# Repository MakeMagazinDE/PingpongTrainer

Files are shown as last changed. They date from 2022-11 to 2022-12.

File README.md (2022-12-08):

GitHub Logo

Maker Media GmbH

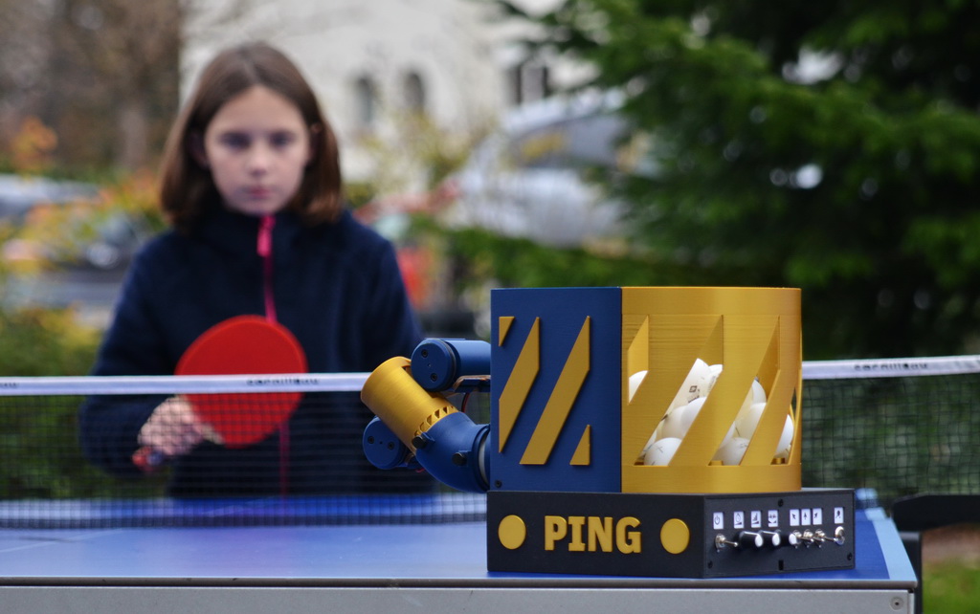
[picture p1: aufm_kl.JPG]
Aufmacher


# Pingpong-Trainingroboter

Tischtennis beinhaltet alles, was ein gutes Freizeitspiel ausmacht: Geschick und Bewegung, Wettbewerb und Spaß, Action und Geselligkeit. Wenn letztere einmal ausfällt, hilft unser Pingpong-Trainingsroboter, der automatisch Bälle in wechselnde Richtungen verschießt.

**Bitte beachten Sie:** Unter **Material** steht im Artikel *Arduino Uno*. Benutzt wird aber ein **Arduino Nano**!

Eine Schritt-für-Schritt-Bauanleitung steht als PDF zu Verfügung, da der Artikel aus Platzgründen nicht alle Aspekte des Aufbaus behandeln konnte.

Stückliste und Verdrahtung siehe Excel-Sheet **Bauteile_und_Verbindungen.xlsx** (Datei mit als "View Raw" oder "Download" herunterladen). Die Excel-Arbeitsmappe wurde auch als PDF konvertiert, ist hier aber unter Umständen nicht mehr gut lesbar.

Ein Video vom Pingpong-Trainingsroboter ist inzwischen hier auf Youtube zu finden: https://youtu.be/tKqPbJfTlDg

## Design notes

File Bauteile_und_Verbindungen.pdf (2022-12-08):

Einkaufsliste

Material | Anzahl | Einzelpreis | Total | Lieferant | Link | Hinweis
Servo MG90s, 180° (digital) | 1 € | 1.99 € | 1.99 AliExpress | https://de.aliexpress.co (https://de.aliexpress.com/item/1005003620828597.html?curPageLogUid=8dz3BZQSF9wu) Bestelldetails siehe Bild.
DC Motor 380, 12V/8'000 RPM, 24V/16'000 RMP | | 2 € | 0.61 € | 1.22 AliExpress | https://de.aliexpress.co (https://de.aliexpress.com/item/32664338955.html)
DC Motor S30K, 12V/14 RPM | 1 € | 1.34 € | 1.34 AliExpress | https://de.aliexpress.co (https://de.aliexpress.com/item/32819069437.html) Bestelldetails siehe Bild
Potentiometer WH148, 10kOhm | 3 | € | 1.14 AliExpress | https://de.aliexpress.co (https://de.aliexpress.com/item/4000971762879.html) 5 Stück pro Los -> 1 bestellen
Mini Kippschalter, MTS-102 SPDT | 4 | € | 0.96 AliExpress | https://de.aliexpress.co (https://de.aliexpress.com/item/32424649963.html) 5 Stück pro Los -> 1 bestellen
Taster mit LED, grün, ohne Symbol, 12mm, Momentary self-reset, 5V | 1 € | 0.75 € | 0.75 AliExpress | https://de.aliexpress.co (https://de.aliexpress.com/item/4001291695467.html) Bestelldetails siehe Bild
NANO Expansion Prototyp Schild I/O R3 | 1 € | 1.06 € | 1.06 AliExpress | https://de.aliexpress.co (https://de.aliexpress.com/item/32836369656.html) Farbe egal. Die rote Version finde ich etwas übersichtlicher, da die Pins
| | | | | | farbcodiert sind.
Terminal Block KF128-2.54, 4 Pins | 1 € | 1.47 € | 1.47 AliExpress | https://de.aliexpress.co Es kann auch ein 6 Pin Terminal bestellt werden, um gleich die ganze Reihe
| | | | | | der Steckplätze zu bestücken. 5 Stücke pro Los -> 1 bestellen
Arduino Nano 328p mit angelöteten Pins | 1 € | 4.42 € | 4.42 AliExpress | https://de.aliexpress.co (https://de.aliexpress.com/item/1005003041312268.html?ad_pvid=202207231457511969517035539440007786855_3&s=p) Empfohlen: Version 328p mit USB-C und bereits angelöteten Pins.
| | | | | | Bestelldetails siehe Bild.
Motortreiber L298N, rot | 2 € | 0.89 € | 1.78 AliExpress | https://de.aliexpress.co (https://de.aliexpress.com/item/32969673726.html) Die Schublade hat nur Bohrlöcher passend für die rote Version!
Micro Limit Switch, ZW12-B | 1 € | 0.76 € | 0.76 AliExpress | https://de.aliexpress.co (https://de.aliexpress.com/item/10000284039075.html) 5 Stücke pro Los -> 1 bestellen
Step Up Converter MT3608 | 1 € | 1.94 € | 1.94 AliExpress | https://de.aliexpress.co (https://de.aliexpress.com/item/4001066566291.html) USB nicht notwendig.
Batteriehalter, 6xAA | | 1 € | 0.22 € | 0.22 AliExpress | https://de.aliexpress.co (https://de.aliexpress.com/item/1005002013461693.html)
Dichtungsring (NBR O-Ring) OD 40mm, ID 28mm, 6mm, black | 2 | € | 1.89 AliExpress | https://de.aliexpress.co 5 Stücke pro Los -> 1 bestellen
Kabel DuPont, beidseitig female/Buchsen, 30cm | | | € | 1.44 AliExpress | https://de.aliexpress.co (https://de.aliexpress.com/item/32639799546.html)
Kabel DuPont, beidseitig female/Buchsen, 10cm | € | 0.93 AliExpress | https://de.aliexpress.co (https://de.aliexpress.com/item/32422441283.html) Im Verbindungsplan stehen die Kabellängen. Da einige Kabel einseitig verlötet
| | | | | | werden, muss bei einigen Verbindungen das andere Steckerende abgetrennt werden. Die Potentiometer könnten statt mit einem einadrigen auch mit einem dreiadrigen DuPont-Kabel verbunden werden.
Rändelschraube M3x8 | 2 | € | 2.14 AliExpress | https://de.aliexpress.co (https://de.aliexpress.com/item/1005001434315050.html?curPageLogUid=SsNZ1RpAGzNE) 5 Stück pro Los -> 1 bestellen. Notfalls ginge es auch mit 2 "normalen"
| | | | | | Zylinderkopfschrauben.
Schraube M3x8, Senkkopf | 15 | € | - | https://de.aliexpress.co (https://de.aliexpress.com/item/32934186482.html)
Schraube M3x8, Zylinderkopf | 25 | € | - | https://de.aliexpress.co (https://de.aliexpress.com/item/32810872544.html)
Schraube M2 | 2 | € | - | Schraubenlänge ca. 6 mm, oftmals werden die Schrauben mit dem Servo
| | | | | | mitgeliefert.
Schraube M2.5 | 3 | € | - | Schraubenlängen:
| | | | | | 1x ca. 6 mm (oftmals wird die Schrauben mit dem Servo mitgeliefert) 2x ca. 12mm (kürzer geht auch)
Mutter M3, vierkant | 30 | € | - | https://de.aliexpress.co (https://de.aliexpress.com/item/1005001612157787.html)
Gummibänder | 4 | € | -
Litzen (rot, schwarz) | € | -
Ping Pong Bälle | € | -
Stück eines alten Fahrradschlauchs | € | -
€ | 25.45 | 22

Viele der M3 Schrauben passen auch, wenn diese länger oder kürzer sind. Damit eine allfällige Schraubenbestellung aber einfacher geht, können alle M3 Schrauben in 8mm Länge bestellt werden. Die passen immer!

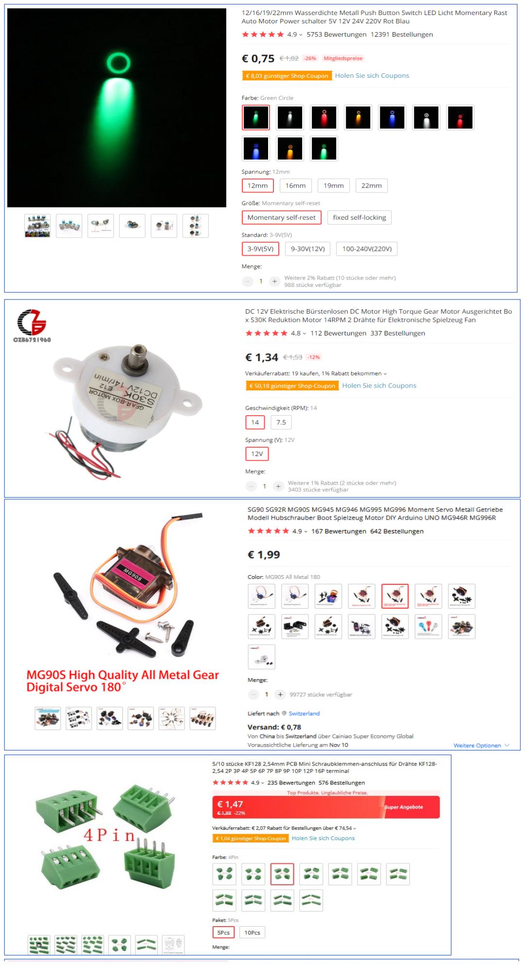
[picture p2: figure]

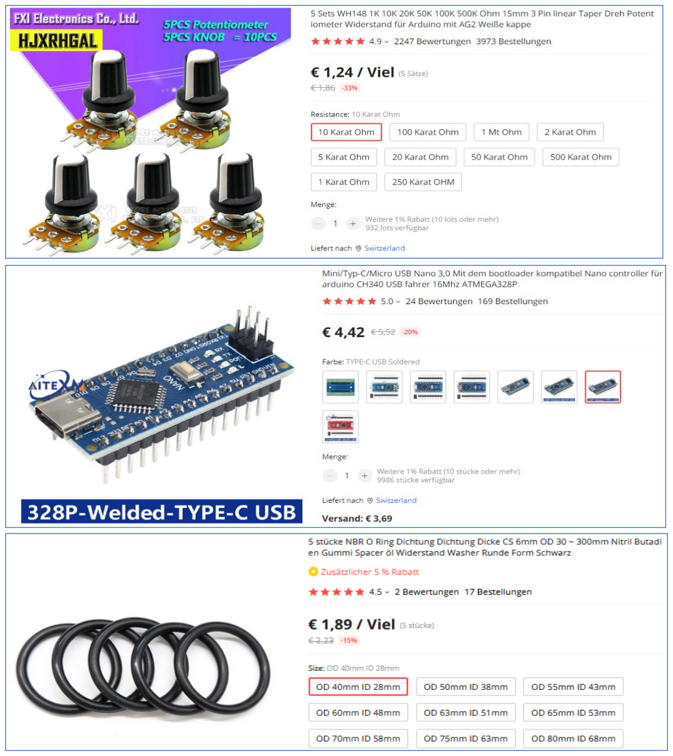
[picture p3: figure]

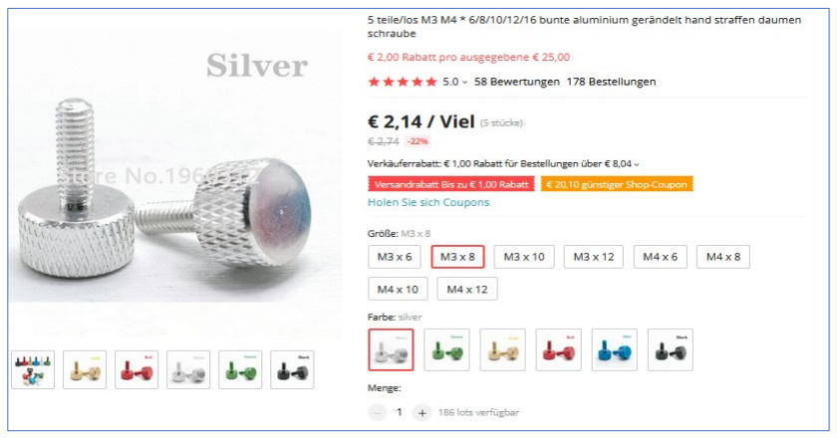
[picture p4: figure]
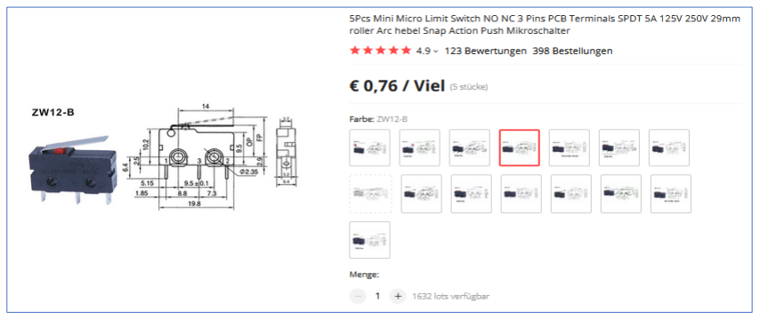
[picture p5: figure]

## Druckbare Bauteile

STL-Datei | 3MF-Datei | Farbvorschlag | Hinweis | Gewicht (g)
AdapterMicroswitch.stl | AdapterMicroswitch.3mf | Schwarz | | 4
AdapterScheibe.stl | AdapterScheibe.3mf | Gelb | | 4
Basis.stl | Basis.3mf | Schwarz | | 308
Biegung 25 Grad.stl | Biegung.3mf | Blau | Optionales Bauteil für flache Bälle. | 20
Biegung 40 Grad.stl | Biegung.3mf | Blau | | 23
Biegung 55 Grad.stl | Biegung.3mf | Blau | Optionales Bauteil für hohe Bälle. | 26
Deko[X].stl | Deko.3mf | Gelb | | 13
Ecke.stl | Ecke.3mf | Blau | | 95
Korb.stl | Korb.3mf | Gelb | Mit Rand drucken für bessere Haftung. | 150
Lauf.stl | Lauf.3mf | Gelb | | 48
Motorschalen[XX].stl, Motoreinsatz.stl | Motorbefestigung.3mf | Blau | Ausrichtung: Runde Öffnung der
| | | Motorbefestigung auf Druckbett liegend.
| | | Motoreinsatz 2x drucken. | 54
Rad[X].stl | Rad.3mf | Blau | Stützen unter den Bohrlöchern bei den
| | | Schraubköpfen von Rad1.stl empfohlen.
| | | Layerhöhe 0.15mm empfohlen. Oberfläche
| | | bügeln empfohlen. Alles zweimal drucken! | 9
Scheibe.stl | Scheibe.3mf | Gelb | | 33
SchriftzugSeite.stl | Schriftzug.3mf | Gelb | Zweimal ausdrucken! | 9
SchriftzugVorne.stl | Schriftzug.3mf | Gelb | | 4
SchubladeBlende.stl | SchubladeBlende.3mf | Schwarz | Ausrichtung: Unbedingt stehend drucken!
| | | Die Blende hat einen kaum sichtbaren
| | | Papiereinschub. Bei falscher
| | | Druckausrichtung lässt sich das Papier für die
| | | Labels später nicht dazwischenschieben.
| | | Drucken eines Randes (Brim) für bessere
| | | Haftung empfohlen. | 33
SchubladeBoden.stl | SchubladeBoden.3mf | Schwarz | | 85
Schwenkarm.stl | Schwenkarm.3mf | Blau | | 10
Servoarm.stl | Servoarm.3mf | Schwarz | Stützen unter dem Bohrloch empfohlen. | 1
Zufuehrung.stl | Zufuehrung.3mf | Blau | | 54
Ergebnis | | | | 983

Generelle Druckanweisungen, anwendbar sofern nicht anders ausgewiesen:
- PLA Filament verwenden
- Layerhöhe 0.3mm / Düsendurchmesser 0.4mm (Standard-Düse)
- Ausrichtung der Bauteile: Siehe Screenshots in der Bauanleitung (Anhang 1)
- Keine Stützen notwendig
- Standardeinstellungen des Slicers führen in der Regel zu einem guten Ergebnis

Für alle Bauteile stehen die 3MF-Dateien zur Verfügung. Wenn du diese Dateien im PrusaSlicer öffnest, ist alles bereits für dich eingestellt. Du brauchst nur noch zu slicen und zu drucken.

Tipps:
- Je nach Filament treten die Drucknähte störend in Erscheinung. Ein schöneres Ergebnis kann immer erzielt werden, wenn die Drucknähte auf eine Kante ausgerichtet sind.
- Innenliegende, kaum sichtbare Bauteile (z.B. AdapterMicroswitch, AdapterScheibe, Servoarm, Schubladenboden) können auch mit Filamentresten beliebiger Farbe gedruckt werden, ohne das Design zu beinträchtigen.
- Basis.stl: Der Druck dieses Bauteils ist etwas anfällig für Warping. Sollten sich die Ecken am Druckboden unschön wölben, sollten entsprechende Massnahmen gegen Verzug angewandt werden. (Onkel Google hilft weiter: Stichwort "3D Druck Warping")
- Stützen unter Bohrlöchern (Servoarm.stl, Rad1.stl) können in der Regel ganz einfach entfernt werden, indem man diese von der anderen Seite durch das Bohrloch herausdrückt.
- Bauteile "Biegung xx Grad.stl": Die angegebene Anzahl Schrauben und Muttern basiert auf der Verwendung von nur einer dieser Bauteilvarianten. Ich empfehle, vorerst nur die Variante mit dem 40 Grad-Winkel zu drucken und zu nutzen. Wer die beiden anderen Winkel für die Schussabgabe später auch verwenden möchte, sollte bei der Materialbestellung zusätzliche Schrauben, Muttern und Rändelschrauben miteinrechnen.
- Beim Druck von Dekoelementen und Schriftzügen drucke ich vielfach nur eine (1) vertikale Konturhülle und lege die Objekte mit der später sichtbaren Aussenseite auf das glatte Druckbett.
- "Elefantenfüsse" können die Passgenauigkeit der Bauteile erschweren. Deshalb sollte eine entsprechende Elefantenfuss-Kompensation beim Druck angewendet werden. (Bei PLA genügt meistens 0.1mm.)
- Wer Filament sparen möchte, kann insbesondere bei den horizontalen, massiven, grossflächigen Schichten einsparen (z.B. bei der Scheibe oder beim Schubladenboden nur zwei massive Bodenschichten drucken.)

## Verbindungsplan

Nr. | Bauteil A | Anschluss Bauteil A | Lötv. A | Verbindung | Lötv. B | Anschluss Bauteil B | Bauteil B | Hinweis
0 Terminal Block KF128 | | Alle Pins | x | Terminal Block auf das Expansion Board stecken und Pins anlöten. | x | VCC, G, G, VIN | NANO I/O Expansion Board | Ist das Terminal angelötet, dann sind die Labels der Anschlüsse auf dem Board nicht mehr sichtbar. Deshalb wird empfohlen, die Anschlüsse am Terminal mit einem Stift anzuschreiben.
1 Batteriefach 6AA | | rote Ader (+) | x | Ader des Batteriefachs direkt an Schalter anlöten. | x | Mittlerer Kontakt | Mini Kippschalter MTS-102 SPDT (Einschalter)
2 Batteriefach 6AA | | schwarze Ader (-) | x | Ader des Batteriefachs direkt an Converter anlöten. | x | VIN- | StepUp Converter MT3608
3 Mini Kippschalter MTS-102 SPDT | (Einschalter) | NO | x | 12cm Kabel (rot) beidseitig anlöten. An diesem Anschluss des Kippschalters werden zwei Verbindungen angebracht: Nr. 3 und 4. --> Am besten gleichzeitig anlöten! | x | VIN+ | StepUp Converter MT3608
4 Mini Kippschalter MTS-102 SPDT | (Einschalter) | NO | x | 20cm Kabel (rot) an Schalter anlöten und am Schraubterminal einschrauben. An diesem Anschluss des Kippschalters werden zwei Verbindungen angebracht: Nr. 3 und 4. --> Am besten gleichzeitig anlöten! | | VIN (Schraubterminal) | NANO I/O Expansion Board
5 Mini Kippschalter MTS-102 SPDT | (Schussrichtung links) | NO | x | 10cm Kabel, DuPont-Buchse einseitig: An Schalter anlöten und am Pin des Boards einstecken. | | A2 (D16) | NANO I/O Expansion Board
6 Mini Kippschalter MTS-102 SPDT | (Schussrichtung links) | Mittlerer Kontakt | x | 10cm Kabel (schwarz), DuPont-Buchse einseitig: An Schalter anlöten und am Pin des Boards einstecken. | | GND | NANO I/O Expansion Board
7 Mini Kippschalter MTS-102 SPDT | (Schussrichtung mitte) | NO | x | 10cm Kabel, DuPont-Buchse einseitig: An Schalter anlöten und am Pin des Boards einstecken. | | A3 (D17) | NANO I/O Expansion Board
8 Mini Kippschalter MTS-102 SPDT | (Schussrichtung mitte) | Mittlerer Kontakt | x | 10cm Kabel (schwarz), DuPont-Buchse einseitig: An Schalter anlöten und am Pin des Boards einstecken. | | GND | NANO I/O Expansion Board
9 Mini Kippschalter MTS-102 SPDT | (Schussrichtung rechts) | NO | x | 10cm Kabel, DuPont-Buchse einseitig: An Schalter anlöten und am Pin des Boards einstecken. | | A4 (D18) | NANO I/O Expansion Board
10 Mini Kippschalter MTS-102 SPDT | (Schussrichtung rechts) | Mittlerer Kontakt | x | 10cm Kabel (schwarz), DuPont-Buchse einseitig: An Schalter anlöten und am Pin des Boards einstecken. | | GND | NANO I/O Expansion Board
11 Micro Limit Switch ZW12-B (Sensor für | Ballvorschub) | NO | x | 40cm Kabel, DuPont-Buchse einseitig: An Schalter anlöten und am Pin des Boards einstecken. Kabel am Micro Limit Switch unbedingt so anlöten, dass diese direkt nach hinten geführt werden können! (Siehe Abbildung im Anhang 2 der Bauanleitung.) | | A0 | NANO I/O Expansion Board | 30cm Kabel wäre auch knapp ausreichend. Die Schublade lässt sich dann aber nicht mehr vollständig ausziehen.
12 Micro Limit Switch ZW12-B (Sensor für | Ballvorschub) | C | x | 40cm Kabel (schwarz), DuPont-Buchse einseitig: An Schalter anlöten und am Pin des Boards einstecken. Kabel am Micro Limit Switch unbedingt so anlöten, dass diese direkt nach hinten geführt werden können! Der Platz im Bauteil AdapterMicroswitch ist knapp! (Siehe Abbildung im Anhang 2 der Bauanleitung.) | | GND | NANO I/O Expansion Board | 30cm Kabel wäre auch knapp ausreichend. Die Schublade lässt sich dann aber nicht mehr vollständig ausziehen.
13 Momentary Switch mit LED (LED) | | Plus (+) | x | 10cm Kabel (rot), DuPont-Buchse einseitig: An Schalter anlöten und am Pin des Boards einstecken. | | D12 | NANO I/O Expansion Board
14 Momentary Switch mit LED (LED) | | Minus (-) | x | 10cm Kabel (schwarz), DuPont-Buchse einseitig: An Schalter anlöten und am Pin des Boards einstecken. | | GND | NANO I/O Expansion Board
15 Momentary Switch mit LED (Startknopf) | | (ohne Beschriftung) | x | 10cm Kabel, DuPont-Buchse einseitig: An Schalter anlöten und am Pin des Boards einstecken. | | A1 | NANO I/O Expansion Board
16 Momentary Switch mit LED (Startknopf) | | (ohne Beschriftung) | x | 10cm Kabel (schwarz), DuPont-Buchse einseitig: An Schalter anlöten und am Pin des Boards einstecken. | | GND | NANO I/O Expansion Board
17 Servo MG90s | GND (braune Ader) | Stecker des Servos direkt mit den Pins des Boards verbinden. | GND | NANO I/O Expansion Board

18 Servo MG90s | V (rote Ader) | | Stecker des Servos direkt mit den Pins des Boards verbinden. | | V | NANO I/O Expansion Board
19 Servo MG90s | Signal (gelbe Ader) | | Stecker des Servos direkt mit den Pins des Boards verbinden. | | D5 | NANO I/O Expansion Board
20 Motortreiber L298N - A | VCC (Schraubterminal) | | 15cm Kabel (rot): Am Terminal des Motortreibers einschrauben und am Converter anlöten. | x | VOUT+ | StepUp Converter MT3608 | Am Anschluss des Motortreibers werden zwei Kabel angebracht -> Nr. 43
21 NANO I/O Expansion Board | GND (Schraubterminal) | | 15cm Kabel (schwarz): Am Terminal des Boards einschrauben und am Converter anlöten. | x | VOUT- | StepUp Converter MT3608 | Das Schraubterminal des Microcontrollers hat zwei GND Anschlüsse. Nimm einfach einen freien Platz.
22 Motortreiber L298N - A | GND (Schraubterminal) | | 5cm Kabel (schwarz): Beidseitig an den Terminals einschrauben. | | GND (Schraubterminal) | NANO I/O Expansion Board | Das Schraubterminal des Microcontrollers hat zwei GND Anschlüsse. Nimm einfach einen freien Platz. Am Anschluss des Motortreibers werden zwei Kabel angebracht -> Nr. 44
23 Motortreiber L298N - A | 5V (Schraubterminal) | | 5cm Kabel (rot): Beidseitig an den Terminals einschrauben. | | 5V (Schraubterminal) | NANO I/O Expansion Board | Am Anschluss des Motortreibers werden zwei Kabel angebracht -> Nr. 45
24 Motortreiber L298N - A | OUT1 (Schraubterminal) | | 60cm Kabel (rot): Am Terminal des Motortreibers einschrauben und am Motor anlöten. | x | Plus | DC Motor 380 (oben)
25 Motortreiber L298N - A | OUT2 (Schraubterminal) | | 60cm Kabel (schwarz): Am Terminal des Motortreibers einschrauben und am Motor anlöten. | x | Minus | DC Motor 380 (oben)
26 Motortreiber L298N - A | OUT4 (Schraubterminal) | | Rote Ader des Motors verlängern auf 30 cm. Verbindungsstelle mit Schrumpfschlauch isolieren. Am Terminal des Motortreibers einschrauben. | x | rote Ader | DC Motor S30K (Vorschub)
27 Motortreiber L298N - A | OUT3 (Schraubterminal) | | Schwarze Ader des Motors verlängern auf 30 cm. Verbindungsstelle mit Schrumpfschlauch isolieren. Am Terminal des Motortreibers einschrauben. | x | schwarze Ader | DC Motor S30K (Vorschub)
28 Motortreiber L298N - A | ENA | | 10cm Kabel beidseitig mit DuPont-Buchse: Pins beidseitig verbinden. | | D11 | NANO I/O Expansion Board
29 Motortreiber L298N - A | IN1 | | 10cm Kabel beidseitig mit DuPont-Buchse: Pins beidseitig verbinden. | | D9 | NANO I/O Expansion Board
30 Motortreiber L298N - A | IN2 | | 10cm Kabel beidseitig mit DuPont-Buchse: Pins beidseitig verbinden. | | D10 | NANO I/O Expansion Board
31 Motortreiber L298N - A | IN3 | | 10cm Kabel beidseitig mit DuPont-Buchse: Pins beidseitig verbinden. | | D7 | NANO I/O Expansion Board
32 Motortreiber L298N - A | IN4 | | 10cm Kabel beidseitig mit DuPont-Buchse: Pins beidseitig verbinden. | | D8 | NANO I/O Expansion Board
33 Motortreiber L298N - A | ENB | | 10cm Kabel beidseitig mit DuPont-Buchse: Pins beidseitig verbinden. | | D6 | NANO I/O Expansion Board
34 Potentiometer (Schussweite) | Anfang (Anschluss aussen) | x | 15cm Kabel (rot), einseitig mit DuPont-Buchse: An Potentiometer anlöten und auf Pin des Boards stecken. | | V | NANO I/O Expansion Board | Diese Verbindung kann auch mit einem dreiadrigen DuPont-Kabel realisiert werden (Nr. 34, 35 und 36).
35 Potentiometer (Schussweite) | Ende (Anschluss aussen) | x | 15cm Kabel (schwarz), einseitig mit DuPont-Buchse: An Potentiometer anlöten und auf Pin des Boards stecken. | | GND | NANO I/O Expansion Board | Diese Verbindung kann auch mit einem dreiadrigen DuPont-Kabel realisiert werden (Nr. 34, 35 und 36).
36 Potentiometer (Schussweite) | Schleifer (Anschluss Mitte) | x | 15cm Kabel, einseitig mit DuPont-Buchse: An Potentiometer anlöten und auf Pin des Boards stecken. | | A6 | NANO I/O Expansion Board | Diese Verbindung kann auch mit einem dreiadrigen DuPont-Kabel realisiert werden (Nr. 34, 35 und 36).
37 Potentiometer (Schussintervall) | Anfang (Anschluss aussen) | x | 15cm Kabel (rot), einseitig mit DuPont-Buchse: An Potentiometer anlöten und auf Pin des Boards stecken. | | V | NANO I/O Expansion Board | Diese Verbindung kann auch mit einem dreiadrigen DuPont-Kabel realisiert werden (Nr. 37, 38 und 39).
38 Potentiometer (Schussintervall) | Ende (Anschluss aussen) | x | 15cm Kabel (schwarz), einseitig mit DuPont-Buchse: An Potentiometer anlöten und auf Pin des Boards stecken. | | | | dreiadrigen DuPont-Kabel realisiert werden (Nr. 37, 38 und 39).
GND | NANO I/O Expansion Board | Diese Verbindung kann auch mit einem

39 Potentiometer (Schussintervall) | Schleifer (Anschluss Mitte) | x | 15cm Kabel, einseitig mit DuPont-Buchse: An Potentiometer anlöten und auf Pin des Boards stecken. | | A5 | NANO I/O Expansion Board | Diese Verbindung kann auch mit einem dreiadrigen DuPont-Kabel realisiert werden (Nr. 37, 38 und 39).
40 Potentiometer (Spin) | Anfang (Anschluss aussen) | x | 15cm Kabel (rot), einseitig mit DuPont-Buchse: An Potentiometer anlöten und auf Pin des Boards stecken. | | V | NANO I/O Expansion Board | Diese Verbindung kann auch mit einem dreiadrigen DuPont-Kabel realisiert werden (Nr. 40, 41 und 42).
41 Potentiometer (Spin) | Ende (Anschluss aussen) | x | 15cm Kabel (schwarz), einseitig mit DuPont-Buchse: An Potentiometer anlöten und auf Pin des Boards stecken. | | GND | NANO I/O Expansion Board | Diese Verbindung kann auch mit einem dreiadrigen DuPont-Kabel realisiert werden (Nr. 40, 41 und 42).
42 Potentiometer (Spin) | Schleifer (Anschluss Mitte) | x | 15cm Kabel, einseitig mit DuPont-Buchse: An Potentiometer anlöten und auf Pin des Boards stecken. | | A7 | NANO I/O Expansion Board | Diese Verbindung kann auch mit einem dreiadrigen DuPont-Kabel realisiert werden (Nr. 40, 41 und 42).
43 Motortreiber L298N - B | VCC (Schraubterminal) | | 10cm Kabel (rot): Beidseitig an den Terminals einschrauben. | | VCC (Schraubterminal) | Motortreiber L298N - A | Am Anschluss des Motortreibers werden zwei Kabel angebracht -> Nr. 20
44 Motortreiber L298N - B | GND (Schraubterminal) | | 10cm Kabel (schwarz): Beidseitig an den Terminals einschrauben. | | GND (Schraubterminal) | Motortreiber L298N - A | Am Anschluss des Motortreibers werden zwei Kabel angebracht -> Nr. 22
45 Motortreiber L298N - B | 5V (Schraubterminal) | | 10cm Kabel (rot): Beidseitig an den Terminals einschrauben. | | 5V (Schraubterminal) | Motortreiber L298N - A | Am Anschluss des Motortreibers werden zwei Kabel angebracht -> Nr. 23
46 Motortreiber L298N - B | IN1 | | 10cm Kabel beidseitig mit DuPont-Buchse: Pins beidseitig verbinden. | | D2 | NANO I/O Expansion Board
47 Motortreiber L298N - B | IN2 | | 10cm Kabel beidseitig mit DuPont-Buchse: Pins beidseitig verbinden. | | D4 | NANO I/O Expansion Board
48 Motortreiber L298N - B | ENA | | 10cm Kabel beidseitig mit DuPont-Buchse: Pins beidseitig verbinden. | | D3 | NANO I/O Expansion Board
49 Motortreiber L298N - B | OUT1 (Schraubterminal) | | 60cm Kabel (rot): Am Terminal des Motortreibers einschrauben und am Motor anlöten. | x | Plus | DC Motor 380 (unten)
50 Motortreiber L298N - B | OUT2 (Schraubterminal) | | 60cm Kabel (schwarz): Am Terminal des Motortreibers einschrauben und am Motor anlöten. | x | Minus | DC Motor 380 (unten)

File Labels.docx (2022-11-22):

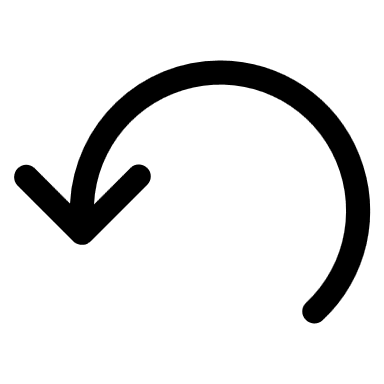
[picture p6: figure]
Linienpfeil: Nach links drehen
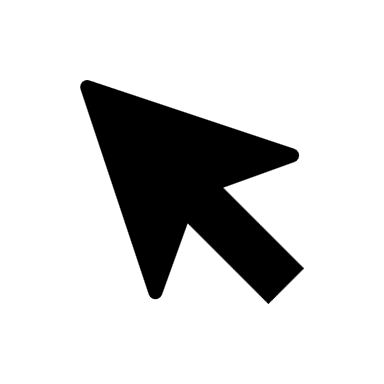
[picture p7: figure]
Cursor
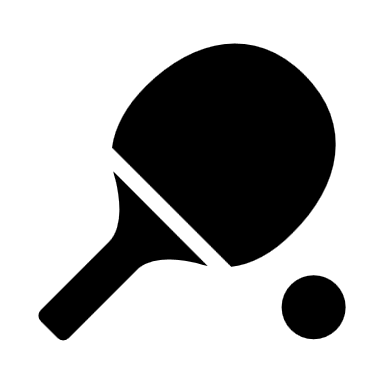
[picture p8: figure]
Tischtennisschläger und -ball
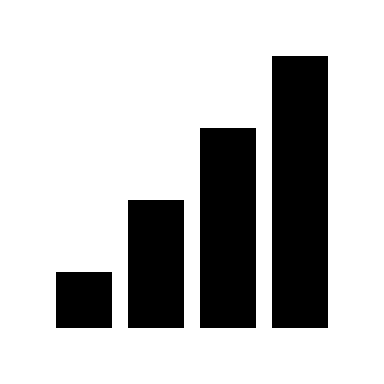
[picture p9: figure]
Signal
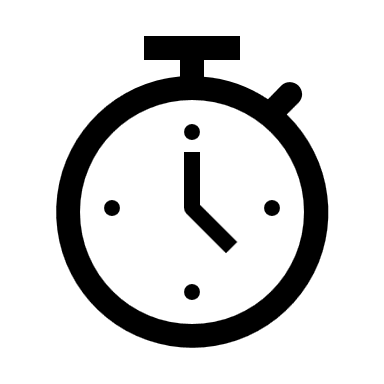
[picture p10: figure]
Stoppuhr
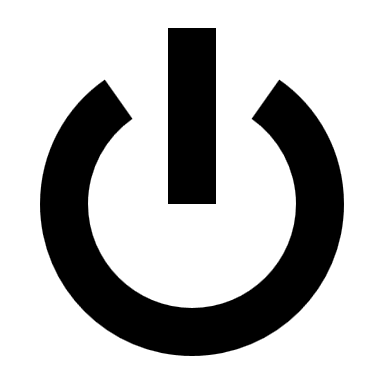
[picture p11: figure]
Ein/Aus
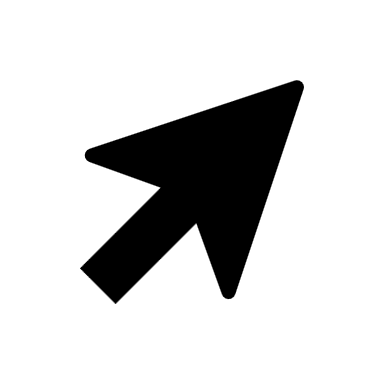
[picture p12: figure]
Cursor

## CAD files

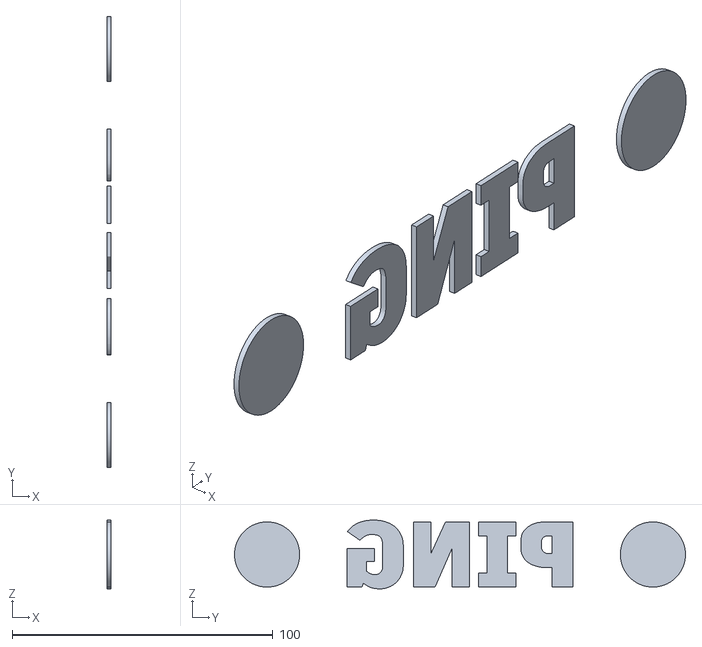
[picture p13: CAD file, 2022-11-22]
3D Druck/SchriftzugSeite.stl
1.50 x 173.0 x 26.4

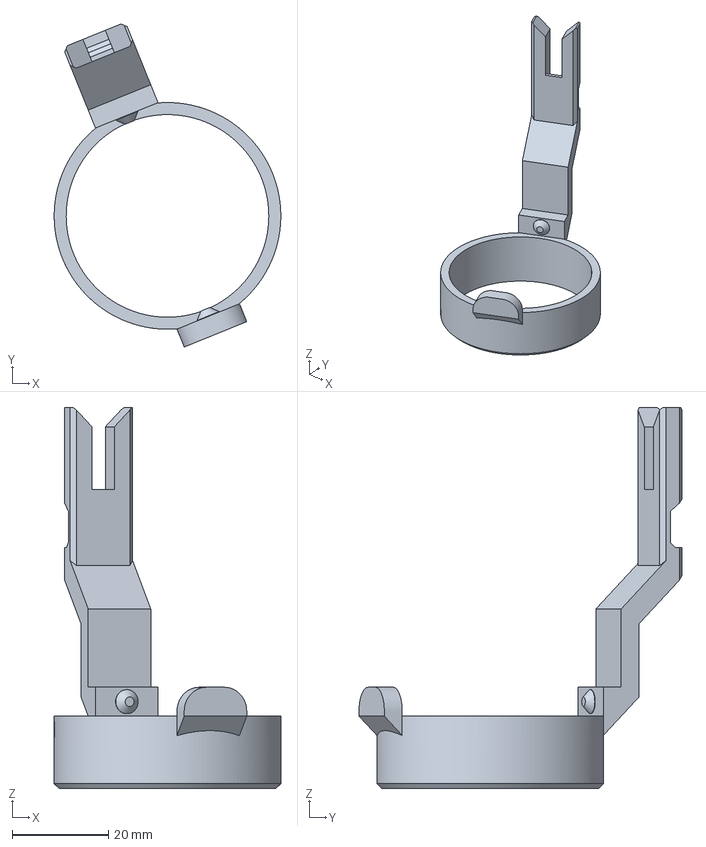
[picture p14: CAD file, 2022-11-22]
3D Druck/Schwenkarm.3mf
47.0 x 67.0 x 79.0 mm

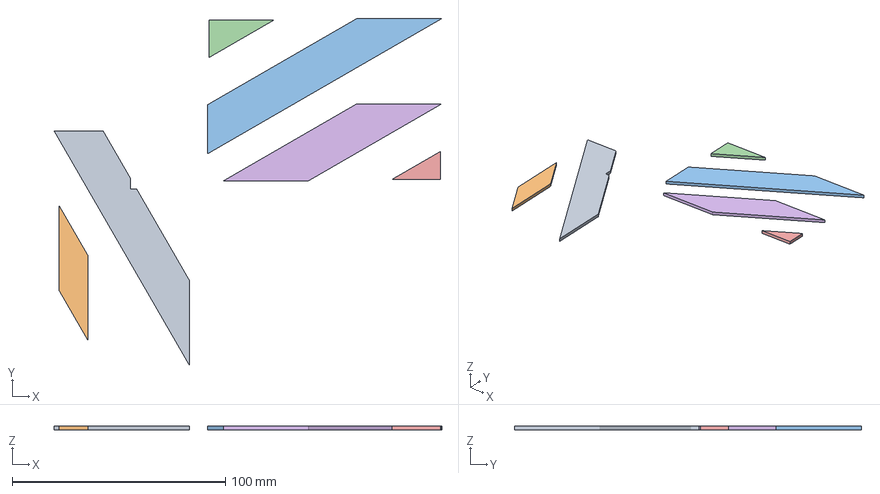
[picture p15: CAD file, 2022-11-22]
3D Druck/Deko.3mf
181.8 x 162.7 x 2.00 mm
Deko2.stl
Deko1.stl
Deko5.stl
Deko6.stl
Deko3.stl
Deko4.stl

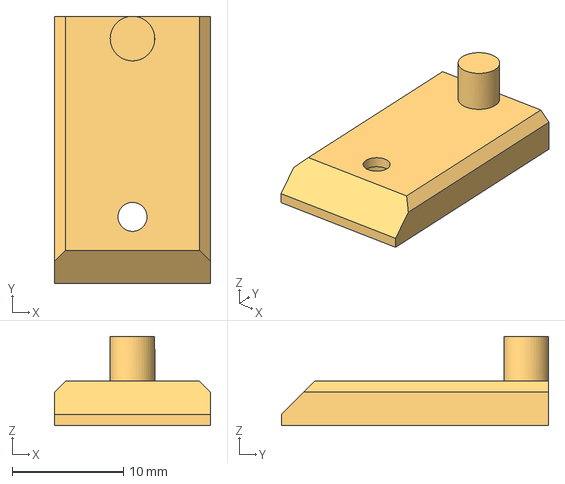
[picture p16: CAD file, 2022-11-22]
3D Druck/Servoarm.step
14.0 x 24.0 x 8.00 mm

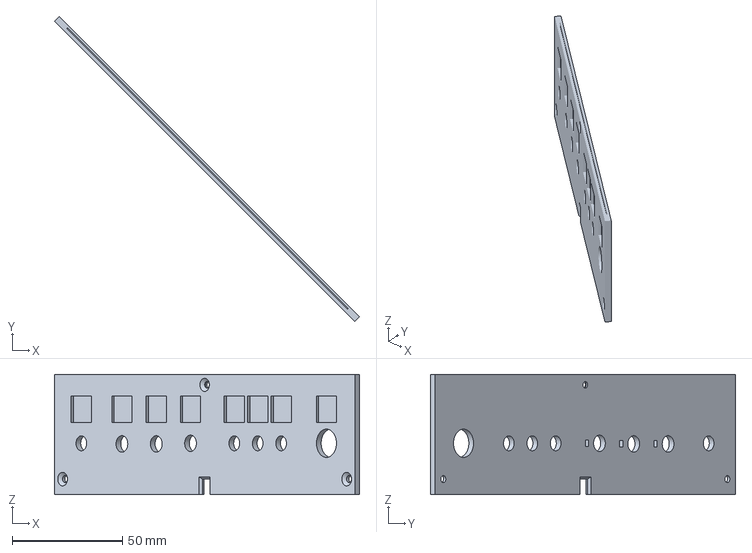
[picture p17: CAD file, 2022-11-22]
3D Druck/SchubladeBlende.3mf
138.2 x 138.2 x 54.4 mm

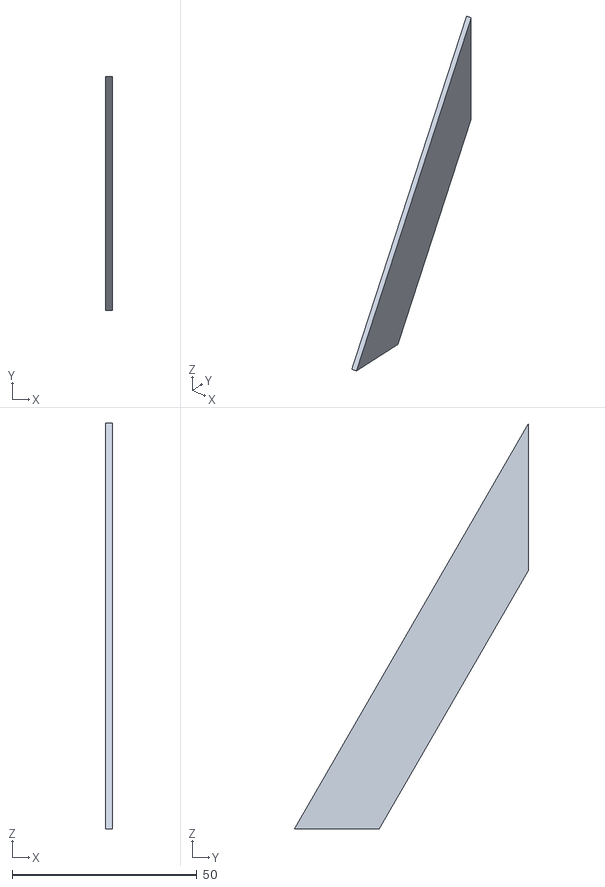
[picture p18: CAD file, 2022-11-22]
3D Druck/Deko5.stl
2.00 x 63.5 x 110.0

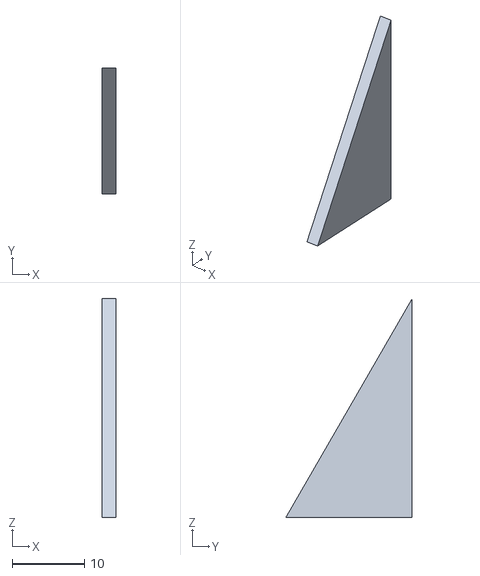
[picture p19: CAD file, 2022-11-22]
3D Druck/Deko6.stl
2.00 x 17.5 x 30.3

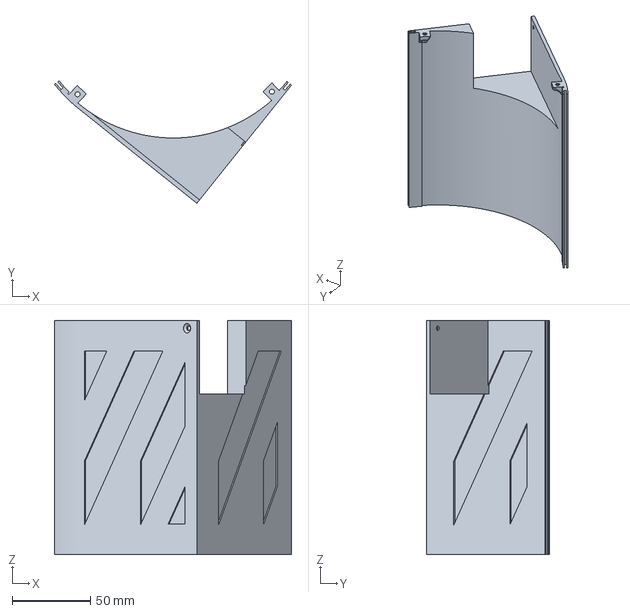
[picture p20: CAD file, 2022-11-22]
3D Druck/Ecke.3mf
151.8 x 78.5 x 150.0 mm

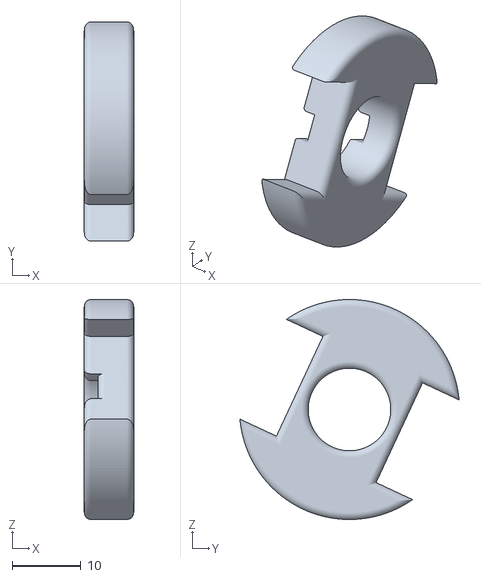
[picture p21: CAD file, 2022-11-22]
3D Druck/Motoreinsatz.stl
7.20 x 31.9 x 32.0

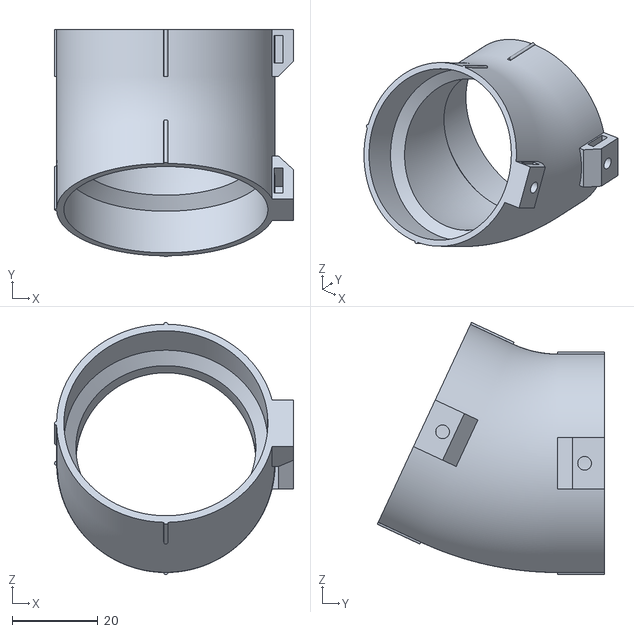
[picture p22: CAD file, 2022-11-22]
3D Druck/Biegung 25 Grad.stl
55.8 x 53.1 x 58.9

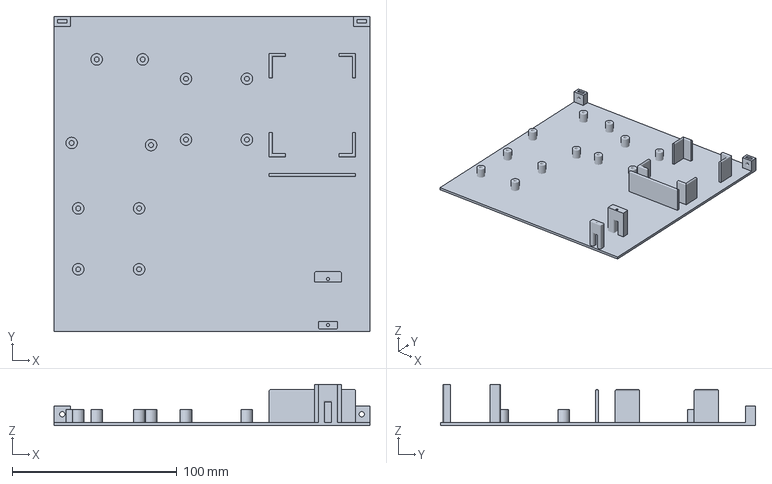
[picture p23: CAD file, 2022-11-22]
3D Druck/SchubladeBoden.3mf
192.0 x 191.5 x 25.2 mm

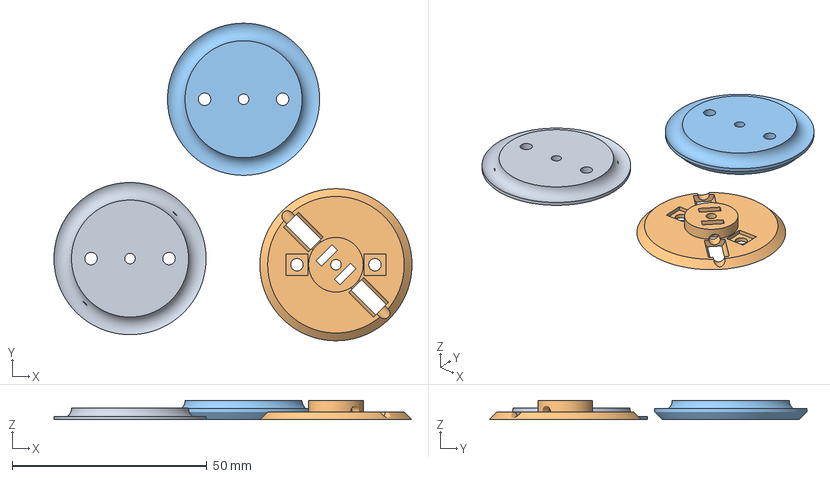
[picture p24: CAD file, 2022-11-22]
3D Druck/Rad.3mf
91.8 x 81.4 x 5.00 mm
Rad2.stl
Rad3.stl
Rad1.stl

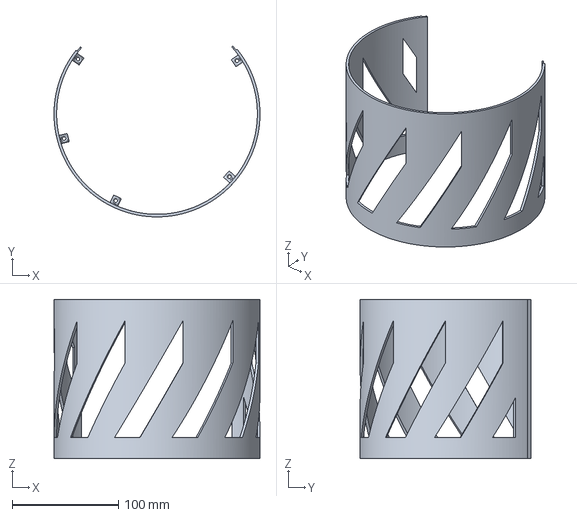
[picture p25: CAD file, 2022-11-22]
3D Druck/Korb.3mf
194.0 x 160.9 x 150.0 mm

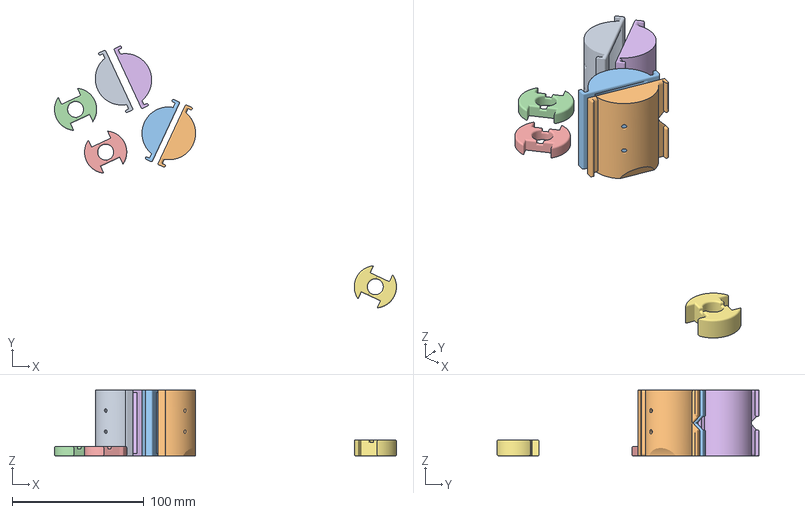
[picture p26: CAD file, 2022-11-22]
3D Druck/Motorbefestigung.3mf
259.1 x 198.3 x 50.0 mm
MotorschaleOU.stl
MotorschaleUO.stl
MotorschaleUU.stl
Motoreinsatz.stl
MotorschaleOO.stl
Motoreinsatz2.stl

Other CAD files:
3D Druck/SchriftzugVorne.stl
3D Druck/Motoreinsatz2.stl
3D Druck/Zufuehrung.3mf
3D Druck/Rad1.stl
3D Druck/AdapterMicroswitch.3mf
3D Druck/AdapterMicroswitch.stl
3D Druck/AdapterScheibe.3mf
3D Druck/AdapterScheibe.stl
3D Druck/Basis.3mf
3D Druck/Basis.stl
3D Druck/Biegung 40 Grad.stl
3D Druck/Biegung 55 Grad.stl
3D Druck/Biegung.3mf
3D Druck/Deko1.stl
3D Druck/Deko2.stl
3D Druck/Deko3.stl
3D Druck/Deko4.stl
3D Druck/Ecke.stl
3D Druck/Korb.stl
3D Druck/Lauf.3mf
3D Druck/Lauf.stl
3D Druck/MotorschaleOO.stl
3D Druck/MotorschaleOU.stl
3D Druck/MotorschaleUO.stl
3D Druck/MotorschaleUU.stl
3D Druck/Rad2.stl
3D Druck/Rad3.stl
3D Druck/Scheibe.3mf
3D Druck/Scheibe.stl
3D Druck/Schriftzug.3mf
3D Druck/SchubladeBlende.stl
3D Druck/SchubladeBoden.stl
3D Druck/Schwenkarm.stl
3D Druck/Servoarm.3mf
3D Druck/Servoarm.stl
3D Druck/Zufuehrung.stl

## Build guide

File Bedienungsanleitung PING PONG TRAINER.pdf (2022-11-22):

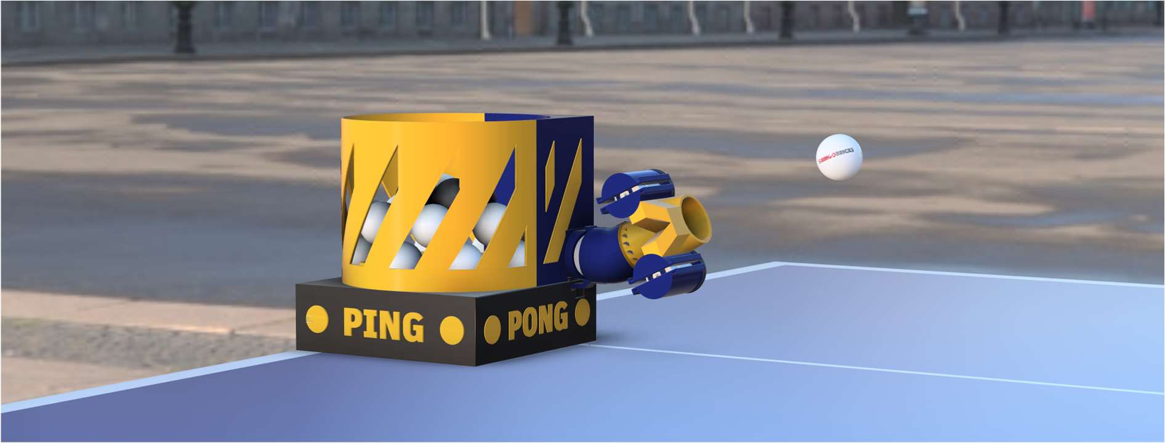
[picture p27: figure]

02. Nov. 2022 | PING PONG TRAINER – Bedienungsanleitung | Seite 1

PING PONG TRAINER

## Bedienungsanleitung

### 1. Vorbereitung

Stelle sicher, dass sechs volle AA Batterien oder entsprechende Akkus im Batteriefach eingelegt sind.
Fülle den Korb mit Ping Pong-Bällen in Standardgrösse (40mm Durchmesser). Der Korb fasst bis zu 60 Bälle!
Stelle den PING PONG TRAINER auf die eine Seite des Tischtennis-Tisches. Du platzierst ihn am besten an der Kante in der Mitte.

Schalte den PING PONG TRAINER am Ein-/Ausschalter ein.

### 2. Intervall, Distanz, Spin und Schussrichtung wählen

Mit dem Regler für das Schussintervall stellst du ein, in welchen Zeitabständen die Bälle geschossen werden. Die blinkende LED des Startbuttons zeigt dir den von dir gewählten Zeitabstand laufend an.

Mit dem Regler für die Schussdistanz stellt du die Schussweite der Bälle ein.

Mit dem Regler für den Spin stellst du die Drallrichtung und Drallstärke der Bälle ein: Rechts: Topspin (Vorwärtsdrall)
Links: Backspin (Rückwärtsdrall)
Mitte: Kein Drall

Mit den Schaltern für die Schussrichtung kannst du wählen, in welche Richtung die Bälle geschossen werden.
Ist der jeweilige Schalter oben, so ist die entsprechende Richtung aktiv.
Sind mehrere Schalter oben, so werden die Bälle reihum in jede aktivierte Richtung geschossen.
Sind alle Schalter unten, also ausgeschaltet, so werden die Richtungen nach Zufallsprinzip ausgewählt!

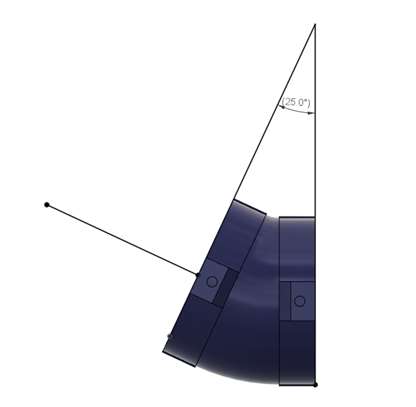
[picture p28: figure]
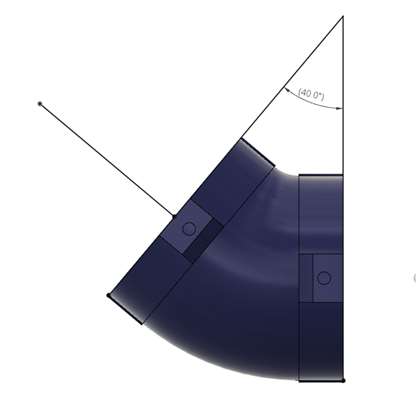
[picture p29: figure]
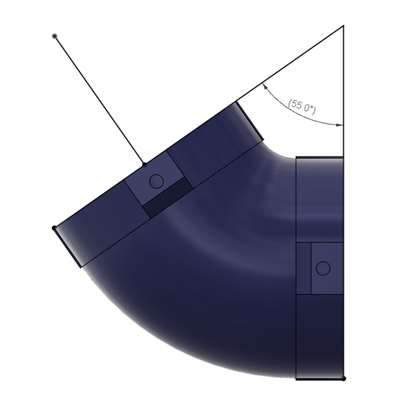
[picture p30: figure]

02. Nov. 2022 | PING PONG TRAINER – Bedienungsanleitung | Seite 2

### 3. Spiel starten / Spiel stoppen

Wenn du den Startknopf drückst, so startet der Motor für die Schussabgabe und die LED leuchtet konstant. Nun bleiben dir einige Sekunden Zeit, um dich auf die gegenüberliegende Seite des Tischtennis-Tisches zu begeben. Anschliessend wird der erste Ball abgefeuert.
Möchtest du das Spiel stoppen, drücke einfach den Startknopf erneut. Ist der Korb leer, schalten die Motoren des PING PONG TRAINERS automatisch ab.

### 4. Flache Bälle / Hohe Bälle

Durch Austausch des gebogenen Mittelstücks kannst du den Winkel der Schussabgabe verändern. Löse die beiden Rändelschrauben, um das Mittelstück zu entfernen und anstelle dessen ein anderes Mittelstück einzusetzen:

Das Mittelstück mit dem

### 25 Grad Winkel

schiesst flache Bälle.

Das Mittelstück mit dem

### 40 Grad Winkel

schiesst mittelhohe Bälle
(empfohlen).

Das Mittelstück mit dem

### 55 Grad Winkel

schiesst hohe Bälle.

Benno Lottenbach, CH-6055 Alpnach Dorf bingobricks@bluewin.ch
https://youtube.com/@BINGOBRICKS

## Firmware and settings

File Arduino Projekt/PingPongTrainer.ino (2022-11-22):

/*
    PING PONG TRAINER
    Software: Version E1.0 - 24.9.2022
    Hardware: Revision E  - 18.9.2022
    YouTube: https://www.youtube.com/channel/UCTQz_JDB3c2g9OMSX82BWHg











    ******************************************************************************
    MIT License

    Copyright (c) 2022 Benno Lottenbach, BINGOBRICKS Switzerland

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
    THE SOFTWARE IS PROVIDED "AS IS", WITHOUT WARRANTY OF ANY KIND, EXPRESS OR
    IMPLIED, INCLUDING BUT NOT LIMITED TO THE WARRANTIES OF MERCHANTABILITY,
    FITNESS FOR A PARTICULAR PURPOSE AND NONINFRINGEMENT. IN NO EVENT SHALL THE
    AUTHORS OR COPYRIGHT HOLDERS BE LIABLE FOR ANY CLAIM, DAMAGES OR OTHER
    LIABILITY, WHETHER IN AN ACTION OF CONTRACT, TORT OR OTHERWISE, ARISING FROM,
    OUT OF OR IN CONNECTION WITH THE SOFTWARE OR THE USE OR OTHER DEALINGS IN THE
    SOFTWARE.
    ******************************************************************************
*/
#include <Servo.h>
#include <Toggle.h>

//Servo deklarieren
#define cServoPin 5
#define cServoPosLeft 160           //Servoposition für Schussrichtung links
#define cServoPosCenter 90          //Servoposition für Schussrichtung mitte
#define cServoPosRight 20           //Servoposition für Schussrichtung rechts
int vServoPos;                      
byte vMoveServo = false;
Servo myServo;

// Motor B1 (Backspin) deklarieren
#define cMB1Pin 3                       // ENA -> PWM notwendig  
#define cMB1In1Pin 2                    // INB / IN2
#define cMB1In2Pin 4                    // INA / IN1
#define cMB1Throttle 0.50               // Faktor, mit welchem die Leistung des Motors gedrosselt wird. Beispiel: Bei 24V Versorgungsspannung und cMB1Throttle = 0.5 -> Am Motor liegen maximal 12V an. Falls die Schussweite trotz maximal offenem Drehregler nicht ausreicht, kann dieser Wert bis maximal auf 1 erhöht werden.
bool vMB1Invert = false;                // Auf true setzen, wenn die Drehrichtung des Motors umgekehrt werden soll
byte vMB1State = LOW;                   // Motor startet, sobald diese Variable auf HIGH ist

// Motor A1 (Topspin) deklarieren
#define cMA1Pin 11                      // ENA -> PWM notwendig  
#define cMA1In1Pin 10                   // INB / IN2
#define cMA1In2Pin 9                    // INA / IN1
#define cMA1Throttle 0.50               // Faktor, mit welchem die Leistung des Motors gedrosselt wird. Beispiel: Bei 24V Versorgungsspannung und cMB1Throttle = 0.5 -> Am Motor liegen maximal 12V an. Falls die Schussweite trotz maximal offenem Drehregler nicht ausreicht, kann dieser Wert bis maximal auf 1 erhöht werden.
bool vMA1Invert = false;                // Auf true setzen, wenn die Drehrichtung des Motors umgekehrt werden soll
byte vMA1State = LOW;                   // Motor startet, sobald diese Variable auf HIGH ist

// Motor A2 (Ballzuführung) deklarieren
#define cMA2Pin 6                       // ENB -> PWM notwendig        
#define cMA2In3Pin 7                    // INC / IN3
#define cMA2In4Pin 8                    // IND / IN4
#define cMA2Throttle 0.50               // Faktor, mit welcher die Leistung von Motor A2 (Ballzuführung) gedrosselt wird. Beispiel: 12V Motor an 24V Versorgungsspannung -> cMA2Throttle = 0.5. Achtung: Ein zu hoher Wert könnte den Motor zerstören!
bool vMA2Invert = false;                // Auf true setzen, wenn die Drehrichtung des Motors umgekehrt werden soll
byte vMA2State = LOW;                   // Motor startet, sobald diese Variable auf HIGH ist
unsigned long vLastMotorstart = 0;      //Enthält den Timestamp, an welchem letztmals die Ballzufuhr gestartet wurde.

//Schalter und Buttons deklarieren
#define cSwitchLeftPin A2
#define cSwitchCenterPin A3
#define cSwitchRightPin A4
#define cSwitchLimitPin A0
#define cButtonStartPin A1
Toggle buttonStart(cButtonStartPin);
Toggle limitSwitch(cSwitchLimitPin);
unsigned long vLastShot = 0;          //Enthält den Timestamp, an welchem letztmals der Limitsensor ausgelöst wurde

//LED deklarieren
#define cLedPin 12
#define cLedDuration 300              //Leuchtdauer der LED für 1x blinken
#define cLedOffset 500                //Offset für das Blinkintervall der LED, weil die benötigte Zeit für den Ballvorschub miteingerechnet werden sollte.
byte vLedState = LOW;
unsigned long vLastBlink = 0;

//Potentiometer deklarieren
#define cPotIntervallPin A5
#define cPotDistancePin A6
#define cPotSpinPin A7
#define cPowerCenterSpin 0.7          //Bei Nullspin reduziert sich die Leistung des Motors auf diesen Prozentwert (bei Fullspin wird auf 100% erhöht)
int vPotDistance = 0;
int vPotIntervall = 0;
float vPotSpin = 0.0;

//Weitere Variablen und Konstanten
#define cStartDelay 5000              //Zeit in ms vom Drücken des Startbuttons bis zur ersten Schussabgabe vergehen soll. (Damit sich der Spieler in Position bringen kann.)
#define cStopDelay 6000               //Zeitlimite in ms, die zwischen zwei Schussabgaben maximal verstreichen darf, bis die Ballzuführung gestoppt wird. 6000 ms entsprechen ca. 1 Umdrehung.
unsigned long vTimeStamp = 0;
byte vState = 0;                      //0 = Standby, 1 = Starting, 2 = Running


void setup() {
  //Serieller Monitor initialisieren
  //Serial.begin(9600);

  //Schalter und Buttons initialisieren
  pinMode(cSwitchLeftPin, INPUT_PULLUP);
  pinMode(cSwitchCenterPin, INPUT_PULLUP);
  pinMode(cSwitchRightPin, INPUT_PULLUP);
  pinMode(cSwitchLimitPin, INPUT_PULLUP);
  pinMode(cButtonStartPin, INPUT_PULLUP);
  buttonStart.begin(cButtonStartPin);
  buttonStart.setToggleState(0);    // set initial state 0 or 1
  buttonStart.setToggleTrigger(0);  // set trigger onPress: 0, or onRelease: 1
  limitSwitch.begin(cSwitchLimitPin);

  //Motoren initialisieren
  pinMode(cMB1Pin, OUTPUT);
  pinMode(cMA1Pin, OUTPUT);
  pinMode(cMA2Pin, OUTPUT);
  pinMode(cMB1In1Pin, OUTPUT);
  pinMode(cMB1In2Pin, OUTPUT);
  pinMode(cMA1In1Pin, OUTPUT);
  pinMode(cMA1In2Pin, OUTPUT);
  pinMode(cMA2In3Pin, OUTPUT);
  pinMode(cMA2In4Pin, OUTPUT);
  digitalWrite(cMB1In1Pin, LOW);
  digitalWrite(cMB1In2Pin, LOW);
  digitalWrite(cMA1In1Pin, LOW);
  digitalWrite(cMA1In2Pin, LOW);
  digitalWrite(cMA2In3Pin, LOW);
  digitalWrite(cMA2In4Pin, LOW);
  analogWrite(cMA2Pin, 255 * cMA2Throttle);
  myServo.attach(cServoPin);

  //Drehregler initialisieren
  pinMode(cPotDistancePin, INPUT);
  pinMode(cPotIntervallPin, INPUT);
  pinMode(cPotSpinPin, INPUT);

  //LED initialisieren
  pinMode(cLedPin, OUTPUT);
  digitalWrite(cLedPin, vLedState);
  pinMode(LED_BUILTIN, OUTPUT);
  
  //Abschluss der Setup-Routine:
  //Servo in allen drei Richtungen positionieren und in der Mitte "parken"
  myServo.write(cServoPosLeft);
  delay(500);
  myServo.write(cServoPosRight);
  delay(500);
  myServo.write(cServoPosCenter);
  //Interne LED 3x kurz blinken lassen
  for (byte i = 0; i < 3; i++) {
    delay(300);
    digitalWrite(LED_BUILTIN, HIGH);
    delay(300);
    digitalWrite(LED_BUILTIN, LOW);
  }
}

void loop() {
  //Serielle Ausgaben zum Debuggen
  //Serial.print(" - StartButton: " + String(digitalRead(cButtonStartPin)));
  //Serial.print(" - ButtonToggle: " + String(buttonStart.toggle()));
  //Serial.print(" - Status: " + String(vState));
  //Serial.print(" - Intervall: " + String(vPotIntervall));
  //Serial.print(" - Distanz: " + String(vPotDistance));
  //Serial.print(" - Spin: " + String(vPotSpin));
  //Serial.print(" - MA1Power: " + String(fGetMPower('A')));
  //Serial.print(" - MB1Power: " + String(fGetMPower('B')));
  //Serial.print(" - LimitPin: " + String(digitalRead(cSwitchLimitPin)));
  //Serial.print(" - LimitOnPress: " + String(limitSwitch.onPress()));
  //Serial.print(" - Ballzufuhr MA2State: " + String(vMA2State));
  //Serial.print(" - Schusss M1State: " + String(vMB1State));
  //Serial.print(" - Servoflag: " + String(vMoveServo));
  //Serial.print(" - Nächste Pos: " + String(vServoPos));
  //Serial.print(" - Links: " + String(digitalRead(cSwitchLeftPin)));
  //Serial.print(" - Mitte: " + String(digitalRead(cSwitchCenterPin)));
  //Serial.print(" - Rechts: " + String(digitalRead(cSwitchRightPin)));
  //Serial.println("");


  fGetPotValues();
  fLedBlink();
  fMotorControl();
  fSetState();
  fState0Standby();
  fState1Ready();
  fState2Running();
}

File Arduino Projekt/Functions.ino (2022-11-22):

//Drehregler auslesen
void fGetPotValues() {
  int vTemp = 0;

  vPotDistance = map(analogRead(cPotDistancePin), 0, 1023, 255, 0);         //Reglerwert von 0-1023 wird auf den Bereich 255-0 umgerechnet
  vPotIntervall = map(analogRead(cPotIntervallPin), 0, 1023, 0, 4000);    //Reglerwert von 0-1023 wird auf den Bereich 0-4000 [ms] umgerechnet
  //vPotSpin = map(analogRead(cPotSpinPin), 0, 1023, 100, -100);                 //Reglerwert von 0-1023 wird auf den Bereich -100% bis +100% umgerechnet
  vTemp = map(analogRead(cPotSpinPin), 0, 1023, 100, -100);                 //Reglerwert von 0-1023 wird auf den Bereich -100 bis +100 umgerechnet
  vPotSpin = vTemp / 100.0;                                               //Die Dezimalstelle hinter dem Komma ist wichtig für die Float-Berechnung!
}

//LED im am Drehregler eingestellten Intervall blinken lassen
void fLedBlink() {
  if (vState != 0) {  //Im Status 1 oder 2 die LED dauernd leuchten lassen.
    vLedState = HIGH;
  } else {  //Ansonsten die LED gemäss dem eingestellten Intervall blinken lassen.
    switch (vLedState) {
      case LOW:
        if ((millis() - vLastBlink) >= (vPotIntervall + cLedOffset)) {
          vLedState = HIGH;
          vLastBlink = millis();
        }
        break;

      case HIGH:
        if ((millis() - vLastBlink) >= cLedDuration) {
          vLedState = LOW;
          vLastBlink = millis();
        }
        break;
    }
  }
  digitalWrite(cLedPin, vLedState);
}

//Motoren anhand der gesetzten Stati und Leistungswerte starten/stoppen
void fMotorControl() {

  if (vMB1Invert) {
    digitalWrite(cMB1In1Pin, vMB1State);
    digitalWrite(cMB1In2Pin, LOW);
  } else {
    digitalWrite(cMB1In1Pin, LOW);
    digitalWrite(cMB1In2Pin, vMB1State);
  }

  if (vMA1Invert) {
    digitalWrite(cMA1In1Pin, LOW);
    digitalWrite(cMA1In2Pin, vMA1State);
  } else {
    digitalWrite(cMA1In1Pin, vMA1State);
    digitalWrite(cMA1In2Pin, LOW);
  }

  if (vMA2Invert) {
    digitalWrite(cMA2In3Pin, vMA2State);
    digitalWrite(cMA2In4Pin, LOW);
  } else {
    digitalWrite(cMA2In3Pin, LOW);
    digitalWrite(cMA2In4Pin, vMA2State);
  }

  //Motoren mit dem errechneten Leistungswert betreiben
  analogWrite(cMA1Pin, fGetMPower('A'));
  analogWrite(cMB1Pin, fGetMPower('B'));

  //Da die Leistung für den Motor 3 (Ballvorschub) immer gleich bleiben soll, wird diese in der Setup-Routine einmalig gesetzt und hier auskommentiert.
  //analogWrite(cMA2Pin, cMA2Throttle);

  //Wenn das MoveServo-Flag gesetzt ist, kann die Servoposition angefahren werden.
  if (vMoveServo) {
    myServo.write(vServoPos);
    vMoveServo = false;
  }
}

byte fGetMPower(char vMotor) {
  byte vMxMax = 0;
  byte vMxMid = 0;
  byte vMxMidToMax = 0;
  byte vMxPower = 0;
  float vPotSpinAbs = 0.0; 

  vPotSpinAbs = fabs(vPotSpin);         //abs() funktioniere nicht bei float-Datentypen. Ich konnte das allerdings nicht nachvollziehen. -> https://github.com/arduino/reference-en/issues/362
  
  vMxMax = vPotDistance;                //Maximale Leistung unter Berücksichtigung der eingestellten Schussweite
  vMxMid = vMxMax * cPowerCenterSpin;   //Leistung bei Nullspin (Mittelposition)
  vMxMidToMax = vMxMax - vMxMid;        //Leistungssteigerung von Nullspin bis Fullspin

  switch (vMotor) {

    case 'A':
      if (vPotSpin >= 0) {
        vMxPower = vMxMid + (vMxMidToMax * vPotSpinAbs);
      } else {
        vMxPower = vMxMid * (1 - vPotSpinAbs);
      }
      vMxPower = vMxPower * cMA1Throttle;
      break;

    case 'B':
      if (vPotSpin >= 0) {
        vMxPower = vMxMid * (1.0 - vPotSpinAbs);
      } else {
        vMxPower = vMxMid + (vMxMidToMax * vPotSpinAbs);
      }
      vMxPower = vMxPower * cMB1Throttle;
      break;
  }

  return vMxPower;
}


//Diese Routine entscheidet, welcher Status gesetzt werden soll.
//Status 0 - Standby - Alle Motoren ausgeschaltet. Das Gerät wartet auf den Start.
//Status 1 - Starting - Der Startknopf wurde gedrückt. Der Benutzer hat nun Zeit, sich an seine Spielposition zu begeben.
//Status 2 - Running - Der Roboter ist in Betrieb und schiesst die Bälle dem Spieler zu.
void fSetState() {

  //Status Startbutton abfragen
  buttonStart.poll();
  if (buttonStart.toggle() == 0) {
    vState = 0;
  }

  if (buttonStart.toggle() == 1) {
    switch (vState) {
      case 0:
        //Start initialisieren:
        vLastMotorstart = 0;                                          //Prüfung auf StopDelay ausschalten
        fDirection();                                                 //erste Servoposition ermitteln
        vMoveServo = true;                                            //Servoflag setzen
        fMotorControl();                                              //Servo positionieren lassen
        vTimeStamp = millis();
        vState = 1;
        break;

      case 1:                                                           //Wenn im Status 1..
        if ((millis() - vTimeStamp) >= cStartDelay) {                   //..mit Start warten, bis Wartezeit verstrichen ist..
          vState = 2;                                                   //...dann Start mit Status 2 auslösen.
        }
        break;

      case 2:                                                           //Wenn im Status 2..
        if (vLastMotorstart > 0) {                                      //..und die Prüfung auf das StopDelay aktiviert ist..
          if (millis() - vLastMotorstart >= cStopDelay) {               //..und der Ballvorschub schon über der Zeitlimite für das StopDelay läuft..
            buttonStart.setToggleState(0);                              //..dann den Stopp-Knopf (virtuell) drücken..
            vState = 0;                                                 //..und den Status auf Standby 0 setzen.
          }
        }
        break;
    }
  }
}



void fState0Standby() {
  if (vState == 0) {  //Standby
    //Alle Motoren stoppen
    vMB1State = LOW;
    vMA1State = LOW;
    vMA2State = LOW;

    //Servo in der Mitte positionieren lassen
    vServoPos = cServoPosCenter;
    vMoveServo = true;
  }
}


void fState1Ready() {
  if (vState == 1) {            //Diese Anweisungen werden mehrmals durchlaufen, solange der Status 1 ist
    vMB1State = HIGH;            //Schussmotor B1 laufen lassen
    vMA1State = HIGH;            //Schussmotor A1 laufen lassen
  }
}
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
